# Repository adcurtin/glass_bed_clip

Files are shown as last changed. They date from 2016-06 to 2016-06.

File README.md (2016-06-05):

# Glass Bed Clip

This is a clip to allow for easily swappable glass beds on a Powerspec 3D Pro printer (a clone of the FlashForge Creator Pro, which is a clone of the Replicator 1).

# Printing

I print at 90% infill (do not print at 100%, you need a little flexibility).  
use supports.  
0.2mm layer height is just fine.  

Print two copies of backboard.stl and one of glass_bed_clip.stl (all 3 parts).

**Do not move or reorient the clips**, they are very sensitive to 'grain' direction and layer orientation.

# Use

I put the 2 backboards on the back corners of the bed. I put the multi piece clip on the front left corner (but front right works too).

the side of the clip that goes toward the bed has 2 things that jut out. The bottom one goes below the bed, and keeps the clips from riding too high above the bed. The top one goes right on top of the metal bed and pushes against the side of the glass.

Below the bed, I have a spring that goes between the two long columns that stick out below the clips. Below the spring is the 3rd piece from glass_bed_clip.stl, the lever. This is so the spring puts more compression on the top of the clip, rather than twisting the levers toward the bottom of the bed.

I replaced the stock screws that hold the metal plate to the PCB heater with longer ones on the corners with extra stuff installed. I used T-nuts on the bottom of the backboards and the bed clip to really secure them in place.

Both the lever and the below the bed guides are necessary for this clip to work for any length of time, but with both of them, this has been installed on my printer for over a year and still works great.

# Notes

backboard.stl comes is this [thing](https://www.thingiverse.com/thing:537587) on thingiverse and is unmodified by me. The rest of the clip comes from another [thing](https://www.thingiverse.com/thing:645203) on thingiverse, but is very heavily modified.

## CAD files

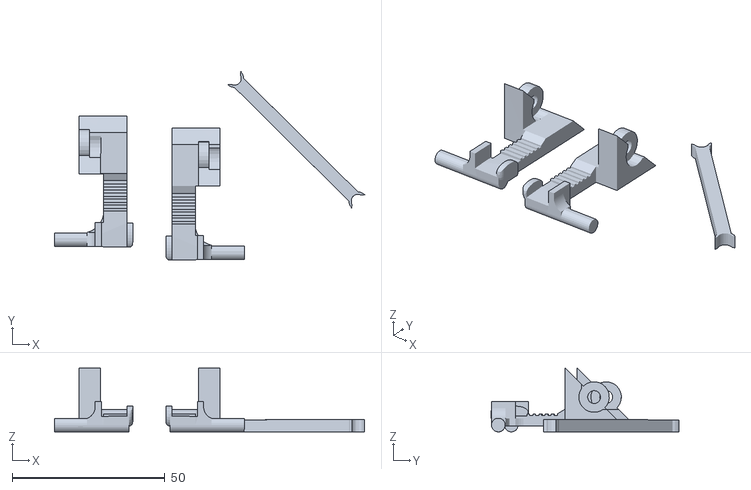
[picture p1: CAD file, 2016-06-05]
glass_bed_clip.stl
101.4 x 61.7 x 20.9

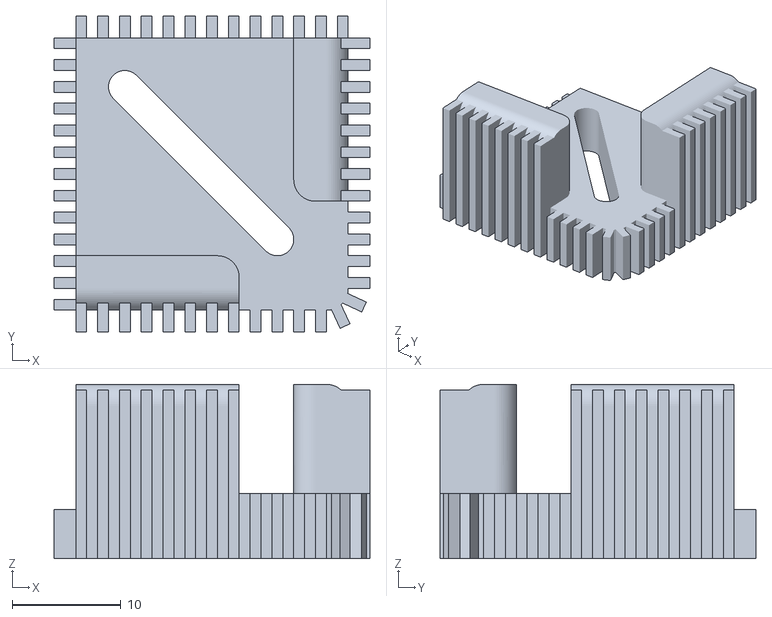
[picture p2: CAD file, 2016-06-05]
backboard.stl
29.0 x 29.0 x 16.0

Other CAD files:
glass_bed_clip.skp
